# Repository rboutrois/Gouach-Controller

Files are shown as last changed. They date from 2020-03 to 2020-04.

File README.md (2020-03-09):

# Gouach controller

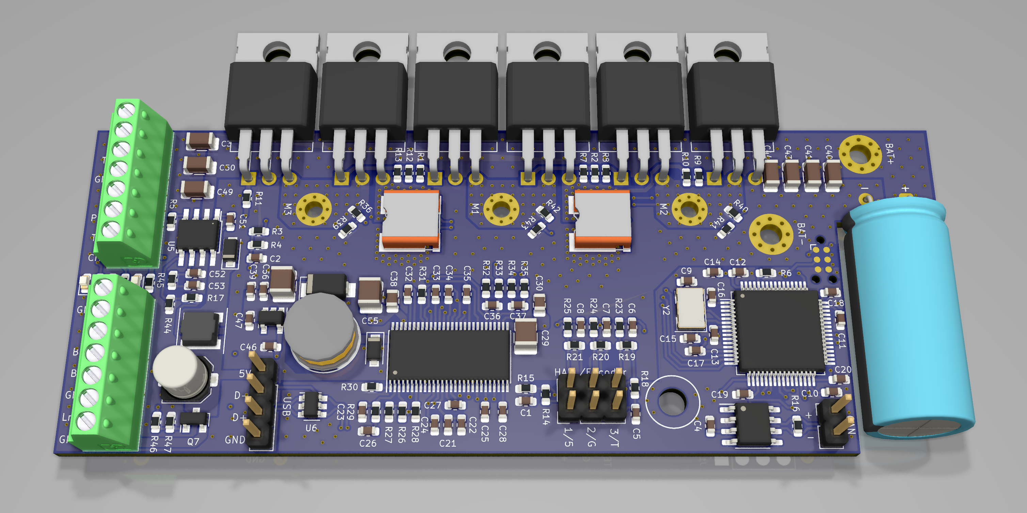
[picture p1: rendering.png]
rendering


## Peripherals pinout
### Throttle
- +5V
- ADC_THROTTLE
- GND

### Torque sensor
- +5V
- PFS
- ADC_TORQUE
- CRUISE
- GND

### Brake
- +5V
- IO_BRAKE
- ADC_BRAKE
- GND

### Motor
3 Phases
- +5V
- HALL_1
- HALL_2
- HALL_3
- TEMPERATURE
- GND

### UART
- +5V
- Tx
- Rx
- GND

### UART
- CAN_H
- CAN_L

### USB
- +5V
- D+
- D-
- GND

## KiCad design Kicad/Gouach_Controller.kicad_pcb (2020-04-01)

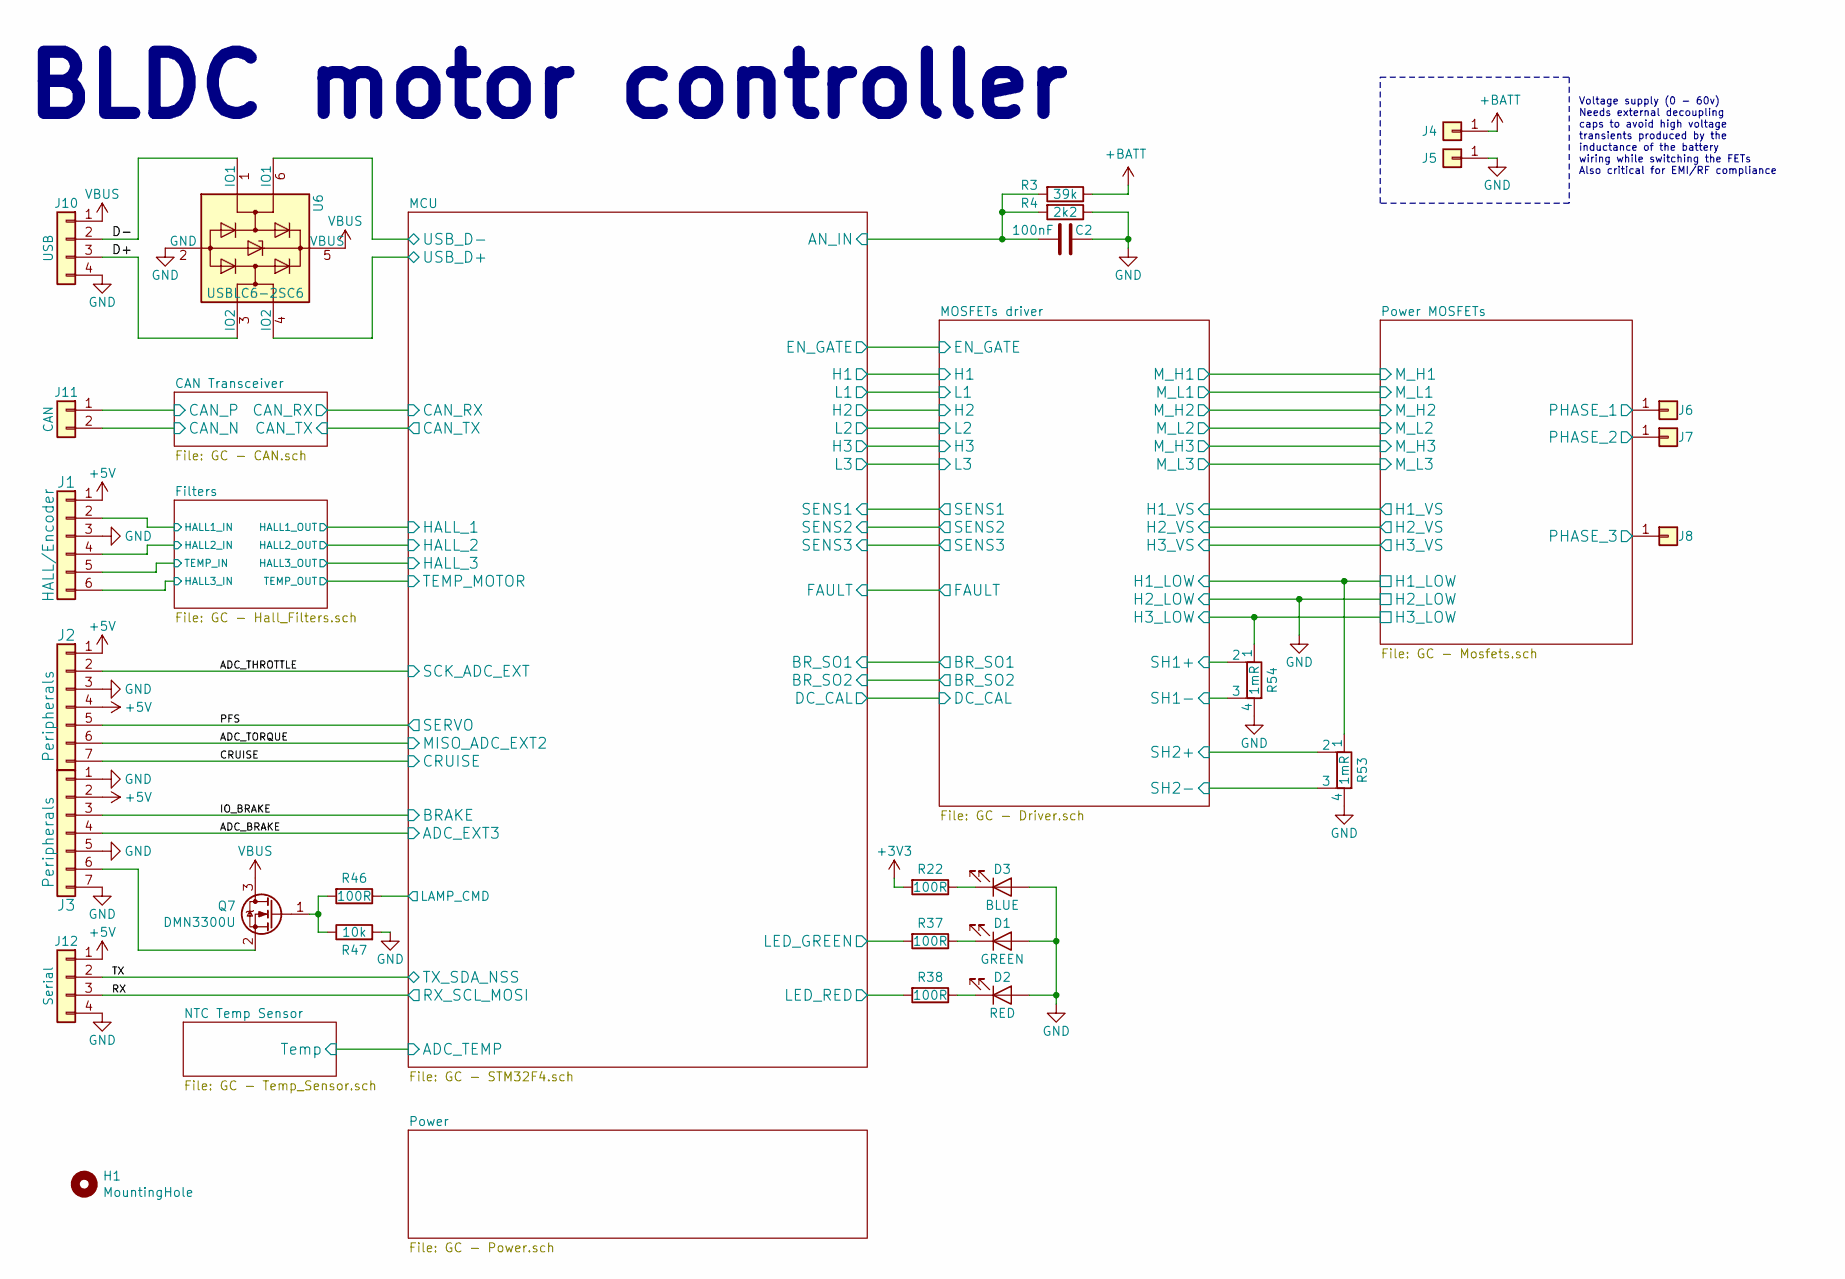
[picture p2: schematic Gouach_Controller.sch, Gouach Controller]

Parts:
C2: 100nF; C_0603_1608Metric
D1: GREEN; LED_0603_1608Metric
D2: RED; LED_0603_1608Metric
D3: BLUE; LED_0603_1608Metric
H1: MountingHole; MountingHole_3.2mm_M3
J1: HALL/Encoder; PinHeader_2x03_P2.54mm_Vertical
J2, J3: Peripherals; TerminalBlock_Phoenix_MPT-2.54mm_7pol
J4: BAT+; MountingHole_2.7mm_Pad_Via
J5: BAT-; MountingHole_2.7mm_Pad_Via
J6: M1; MountingHole_2.2mm_M2_Pad_Via
J7: M2; MountingHole_2.2mm_M2_Pad_Via
J8: M3; MountingHole_2.2mm_M2_Pad_Via
J10: USB; PinHeader_1x04_P2.54mm_Vertical
J11: CAN; PinHeader_1x02_P2.54mm_Vertical
J12: Serial; PinHeader_1x04_P2.54mm_Vertical
Q7: DMN3300U; SOT-23; Mouser 621-DMN3300U-7
R3: 39k; R_0603_1608Metric
R4: 2k2; R_0603_1608Metric
R22, R37, R38, R46: 100R; R_0603_1608Metric
R47: 10k; R_0603_1608Metric
R53, R54: 1mR; WSLP2726; Mouser 71-WSLP27261L000FEA
U6: USBLC6-2SC6; SOT-23-6; Mouser 511-USBLC6-2SC6

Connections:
+3V3: R22.2; also elsewhere on the board
+5V: J1.1, J2.1, J2.4, J3.2, J12.1; also elsewhere on the board
+BATT: J4.1, R3.1; also elsewhere on the board
/ADC_BRAKE: J3.4; also elsewhere on the board
/ADC_THROTTLE: J2.2; also elsewhere on the board
/ADC_TORQUE: J2.6; also elsewhere on the board
/CAN Transceiver/CAN_N: J11.2; also elsewhere on the board
/CAN Transceiver/CAN_P: J11.1; also elsewhere on the board
/CRUISE: J2.7; also elsewhere on the board
/D+: J10.3, U6.3 (IO2)
/D-: J10.2, U6.1 (IO1)
/Filters/HALL1_IN: J1.2; also elsewhere on the board
/Filters/HALL2_IN: J1.4; also elsewhere on the board
/Filters/HALL3_IN: J1.6; also elsewhere on the board
/Filters/TEMP_IN: J1.5; also elsewhere on the board
/IO_BRAKE: J3.3; also elsewhere on the board
/MCU/AN_IN: C2.2, R3.2, R4.2; also elsewhere on the board
/MCU/LAMP_CMD: R46.1; also elsewhere on the board
/MCU/LED_GREEN: R37.2; also elsewhere on the board
/MCU/LED_RED: R38.2; also elsewhere on the board
/MCU/USB_D+: U6.4 (IO2); also elsewhere on the board
/MCU/USB_D-: U6.6 (IO1); also elsewhere on the board
/MOSFETs driver/H1_LOW: R53.1; also elsewhere on the board
/MOSFETs driver/H1_VS: J6.1; also elsewhere on the board
/MOSFETs driver/H2_VS: J7.1; also elsewhere on the board
/MOSFETs driver/H3_LOW: R54.1; also elsewhere on the board
/MOSFETs driver/H3_VS: J8.1; also elsewhere on the board
/MOSFETs driver/SH1+: R54.2; also elsewhere on the board
/MOSFETs driver/SH1-: R54.3; also elsewhere on the board
/MOSFETs driver/SH2+: R53.2; also elsewhere on the board
/MOSFETs driver/SH2-: R53.3; also elsewhere on the board
/PFS: J2.5; also elsewhere on the board
/RX: J12.3; also elsewhere on the board
/TX: J12.2; also elsewhere on the board
GND: C2.1, D1.2 (A), D2.2 (A), D3.2 (A), J1.3, J2.3, J3.1, J3.5, J3.7, J5.1, J10.4, J12.4, R4.1, R47.2, R53.4, R54.4, U6.2 (GND); also elsewhere on the board
unnamed: D1.1 (K), R37.1
unnamed: D2.1 (K), R38.1
unnamed: D3.1 (K), R22.1
unnamed: J3.6, Q7.2 (S)
unnamed: Q7.1 (G), R46.2, R47.1
VBUS: J10.1, Q7.3 (D), U6.5 (VBUS); also elsewhere on the board

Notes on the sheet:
Voltage supply (0 - 60v) Needs external decoupling caps to avoid high voltage transients produced by the inductance of the battery wiring while switching the FETs Also critical for EMI/RF compliance
BLDC motor controller

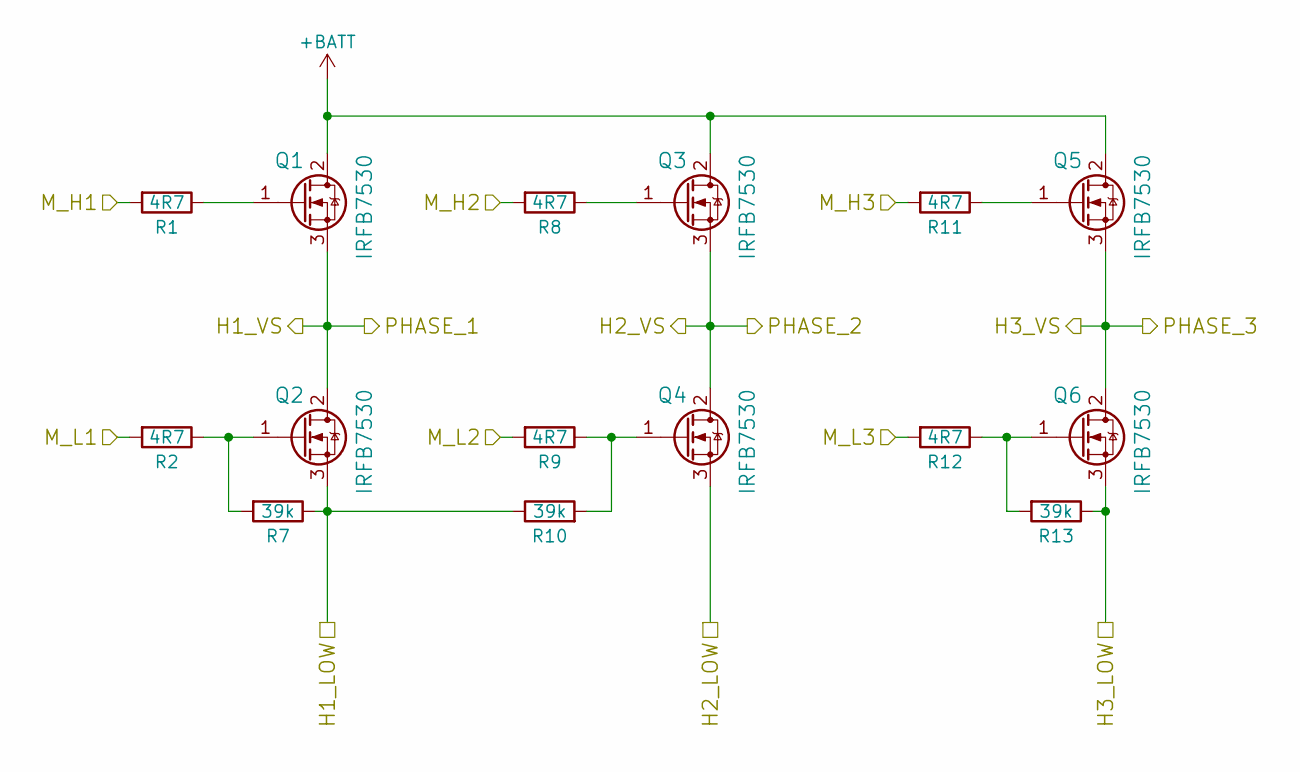
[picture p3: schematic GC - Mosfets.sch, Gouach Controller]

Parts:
Q1, Q2, Q3, Q4, Q5, Q6: IRFB7530; TO-220-3_Horizontal; Mouser 942-IRFB7530PBF
R1, R2, R8, R9, R11, R12: 4R7; R_0603_1608Metric
R7, R10, R13: 39k; R_0603_1608Metric

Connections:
+BATT: Q1.2 (D), Q3.2 (D), Q5.2 (D); also elsewhere on the board
/MOSFETs driver/H1_LOW: Q2.3 (S), R7.1, R10.1; also elsewhere on the board
/MOSFETs driver/H1_VS: Q1.3 (S), Q2.2 (D); also elsewhere on the board
/MOSFETs driver/H2_VS: Q3.3 (S), Q4.2 (D); also elsewhere on the board
/MOSFETs driver/H3_LOW: Q6.3 (S), R13.1; also elsewhere on the board
/MOSFETs driver/H3_VS: Q5.3 (S), Q6.2 (D); also elsewhere on the board
/MOSFETs driver/M_H1: R1.2; also elsewhere on the board
/MOSFETs driver/M_H2: R8.2; also elsewhere on the board
/MOSFETs driver/M_H3: R11.2; also elsewhere on the board
/MOSFETs driver/M_L1: R2.2; also elsewhere on the board
/MOSFETs driver/M_L2: R9.2; also elsewhere on the board
/MOSFETs driver/M_L3: R12.2; also elsewhere on the board
GND: Q4.3 (S); also elsewhere on the board
unnamed: Q1.1 (G), R1.1
unnamed: Q2.1 (G), R2.1, R7.2
unnamed: Q3.1 (G), R8.1
unnamed: Q4.1 (G), R9.1, R10.2
unnamed: Q5.1 (G), R11.1
unnamed: Q6.1 (G), R12.1, R13.2

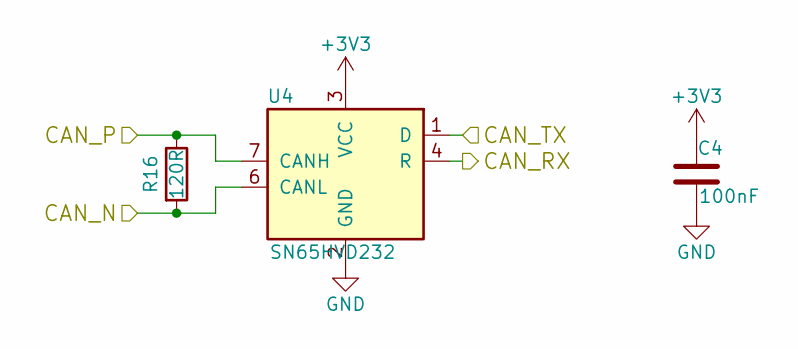
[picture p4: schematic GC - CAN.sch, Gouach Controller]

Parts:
C4: 100nF; C_0603_1608Metric
R16: 120R; R_0603_1608Metric
U4: SN65HVD232; SOIC-8_3.9x4.9mm_P1.27mm; Mouser 595-SN65HVD232DR

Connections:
+3V3: C4.1, U4.3 (VCC); also elsewhere on the board
/CAN Transceiver/CAN_N: R16.2, U4.6 (CANL); also elsewhere on the board
/CAN Transceiver/CAN_P: R16.1, U4.7 (CANH); also elsewhere on the board
/CAN Transceiver/CAN_RX: U4.4 (R); also elsewhere on the board
/CAN Transceiver/CAN_TX: U4.1 (D); also elsewhere on the board
GND: C4.2, U4.2 (GND); also elsewhere on the board

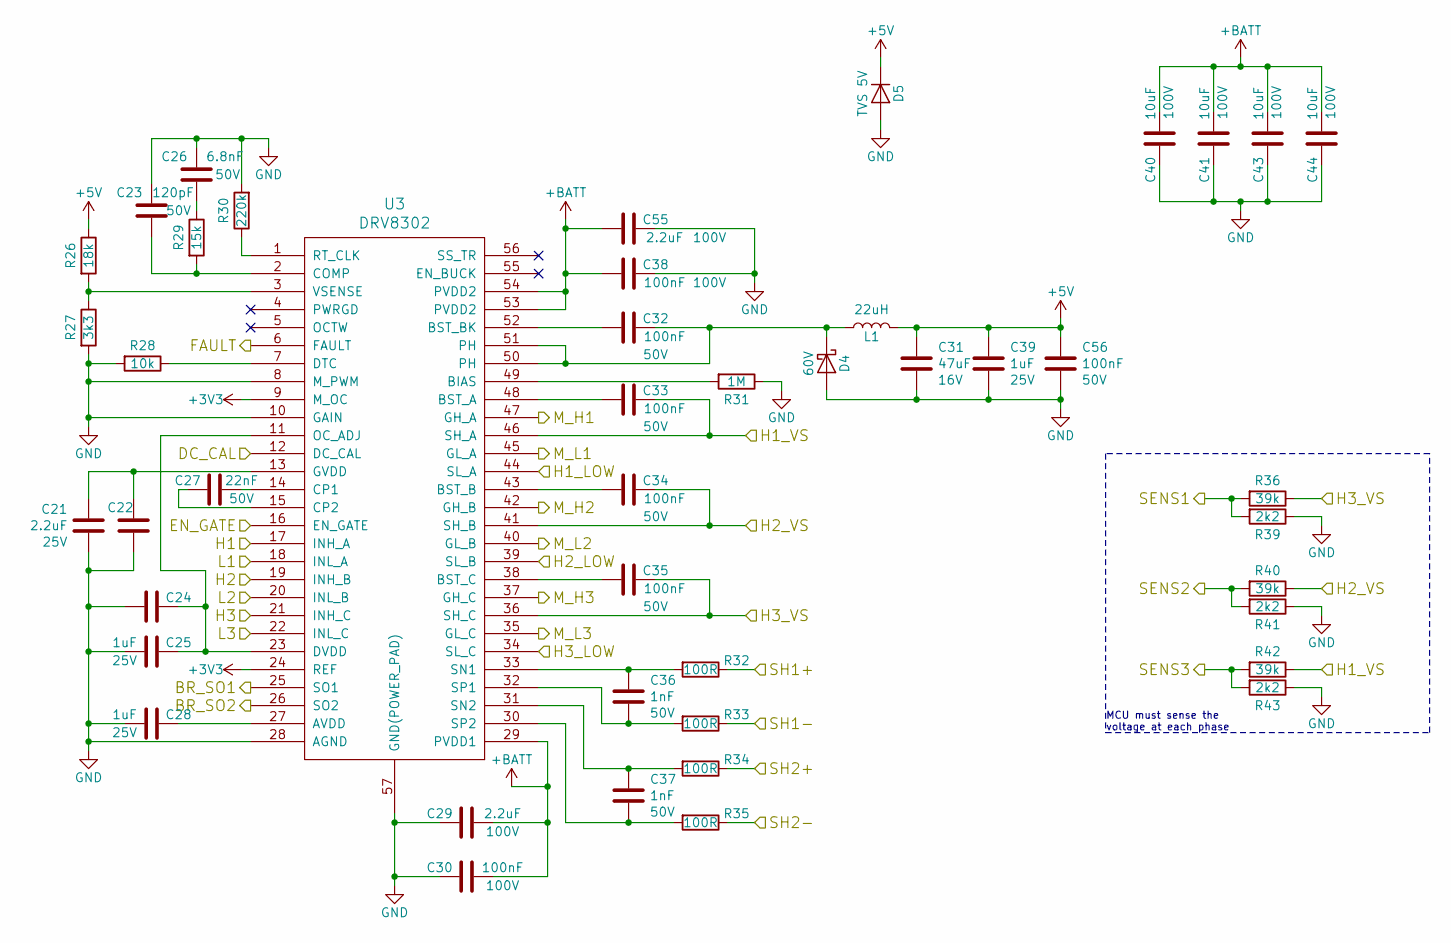
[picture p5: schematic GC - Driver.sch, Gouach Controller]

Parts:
C21: 2.2uF; C_0603_1608Metric
C22, C24: C_0603_1608Metric
C23: 120pF; C_0603_1608Metric
C25, C28, C39: 1uF; C_0603_1608Metric
C26: 6.8nF; C_0603_1608Metric
C27: 22nF; C_0603_1608Metric
C29, C55: 2.2uF; C_1210_3225Metric
C30, C38: 100nF; C_0805_2012Metric
C31: 47uF; C_1210_3225Metric
C32, C33, C34, C35, C56: 100nF; C_0603_1608Metric
C36, C37: 1nF; C_0603_1608Metric
C40, C41, C43, C44: 10uF; C_1206_3216Metric
D4: 60V; D_SOD-123F; Mouser 771-PMEG6020ER-115
D5: TVS 5V; D_SMA; Mouser 652-SMAJ5.0A
L1: 22uH; SDR0805; Mouser 652-SDR0805-220ML
R26: 18k; R_0603_1608Metric
R27: 3k3; R_0603_1608Metric
R28: 10k; R_0603_1608Metric
R29: 15k; R_0603_1608Metric
R30: 220k; R_0603_1608Metric
R31: 1M; R_0603_1608Metric
R32, R33, R34, R35: 100R; R_0603_1608Metric
R36, R40, R42: 39k; R_0603_1608Metric
R39, R41, R43: 2k2; R_0603_1608Metric
U3: DRV8302; Mouser 595-DRV8302DCA

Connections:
+3V3: U3.9 (M_OC), U3.24 (REF); also elsewhere on the board
+5V: C31.1, C39.1, C56.1, D5.1 (K), L1.2, R26.1; also elsewhere on the board
+BATT: C29.1, C30.1, C38.2, C40.1, C41.1, C43.1, C44.1, C55.2, U3.29 (PVDD1), U3.53 (PVDD2), U3.54 (PVDD2); also elsewhere on the board
/MCU/BR_SO1: U3.25 (SO1); also elsewhere on the board
/MCU/BR_SO2: U3.26 (SO2); also elsewhere on the board
/MCU/DC_CAL: U3.12 (DC_CAL); also elsewhere on the board
/MCU/EN_GATE: U3.16 (EN_GATE); also elsewhere on the board
/MCU/FAULT: U3.6 (FAULT); also elsewhere on the board
/MCU/H1: U3.17 (INH_A); also elsewhere on the board
/MCU/H2: U3.19 (INH_B); also elsewhere on the board
/MCU/H3: U3.21 (INH_C); also elsewhere on the board
/MCU/L1: U3.18 (INL_A); also elsewhere on the board
/MCU/L2: U3.20 (INL_B); also elsewhere on the board
/MCU/L3: U3.22 (INL_C); also elsewhere on the board
/MCU/SENS1: R36.2, R39.2; also elsewhere on the board
/MCU/SENS2: R40.2, R41.2; also elsewhere on the board
/MCU/SENS3: R42.2, R43.2; also elsewhere on the board
/MOSFETs driver/H1_LOW: U3.44 (SL_A); also elsewhere on the board
/MOSFETs driver/H1_VS: C33.1, R42.1, U3.46 (SH_A); also elsewhere on the board
/MOSFETs driver/H2_VS: C34.1, R40.1, U3.41 (SH_B); also elsewhere on the board
/MOSFETs driver/H3_LOW: U3.34 (SL_C); also elsewhere on the board
/MOSFETs driver/H3_VS: C35.1, R36.1, U3.36 (SH_C); also elsewhere on the board
/MOSFETs driver/M_H1: U3.47 (GH_A); also elsewhere on the board
/MOSFETs driver/M_H2: U3.42 (GH_B); also elsewhere on the board
/MOSFETs driver/M_H3: U3.37 (GH_C); also elsewhere on the board
/MOSFETs driver/M_L1: U3.45 (GL_A); also elsewhere on the board
/MOSFETs driver/M_L2: U3.40 (GL_B); also elsewhere on the board
/MOSFETs driver/M_L3: U3.35 (GL_C); also elsewhere on the board
/MOSFETs driver/SH1+: R32.1; also elsewhere on the board
/MOSFETs driver/SH1-: R33.1; also elsewhere on the board
/MOSFETs driver/SH2+: R34.1; also elsewhere on the board
/MOSFETs driver/SH2-: R35.1; also elsewhere on the board
GND: C21.2, C22.2, C23.1, C24.1, C25.1, C26.1, C28.1, C29.2, C30.2, C31.2, C38.1, C39.2, C40.2, C41.2, C43.2, C44.2, C55.1, C56.2, D4.2 (A), D5.2 (A), R27.2, R28.2, R30.2, R31.1, R39.1, R41.1, R43.1, U3.8 (M_PWM), U3.10 (GAIN), U3.28 (AGND), U3.39 (SL_B), U3.57 (GND(POWER_PAD)); also elsewhere on the board
unnamed: C21.1, C22.1, U3.13 (GVDD)
unnamed: C23.2, R29.2, U3.2 (COMP)
unnamed: C24.2, C25.2, U3.11 (OC_ADJ), U3.23 (DVDD)
unnamed: C26.2, R29.1
unnamed: C27.1, U3.14 (CP1)
unnamed: C27.2, U3.15 (CP2)
unnamed: C28.2, U3.27 (AVDD)
unnamed: C32.1, D4.1 (K), L1.1, U3.50 (PH), U3.51 (PH)
unnamed: C32.2, U3.52 (BST_BK)
unnamed: C33.2, U3.48 (BST_A)
unnamed: C34.2, U3.43 (BST_B)
unnamed: C35.2, U3.38 (BST_C)
unnamed: C36.1, R32.2, U3.33 (SN1)
unnamed: C36.2, R33.2, U3.32 (SP1)
unnamed: C37.1, R34.2, U3.31 (SN2)
unnamed: C37.2, R35.2, U3.30 (SP2)
unnamed: R26.2, R27.1, U3.3 (VSENSE)
unnamed: R28.1, U3.7 (DTC)
unnamed: R30.1, U3.1 (RT_CLK)
unnamed: R31.2, U3.49 (BIAS)

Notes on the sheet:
MCU must sense the voltage at each phase

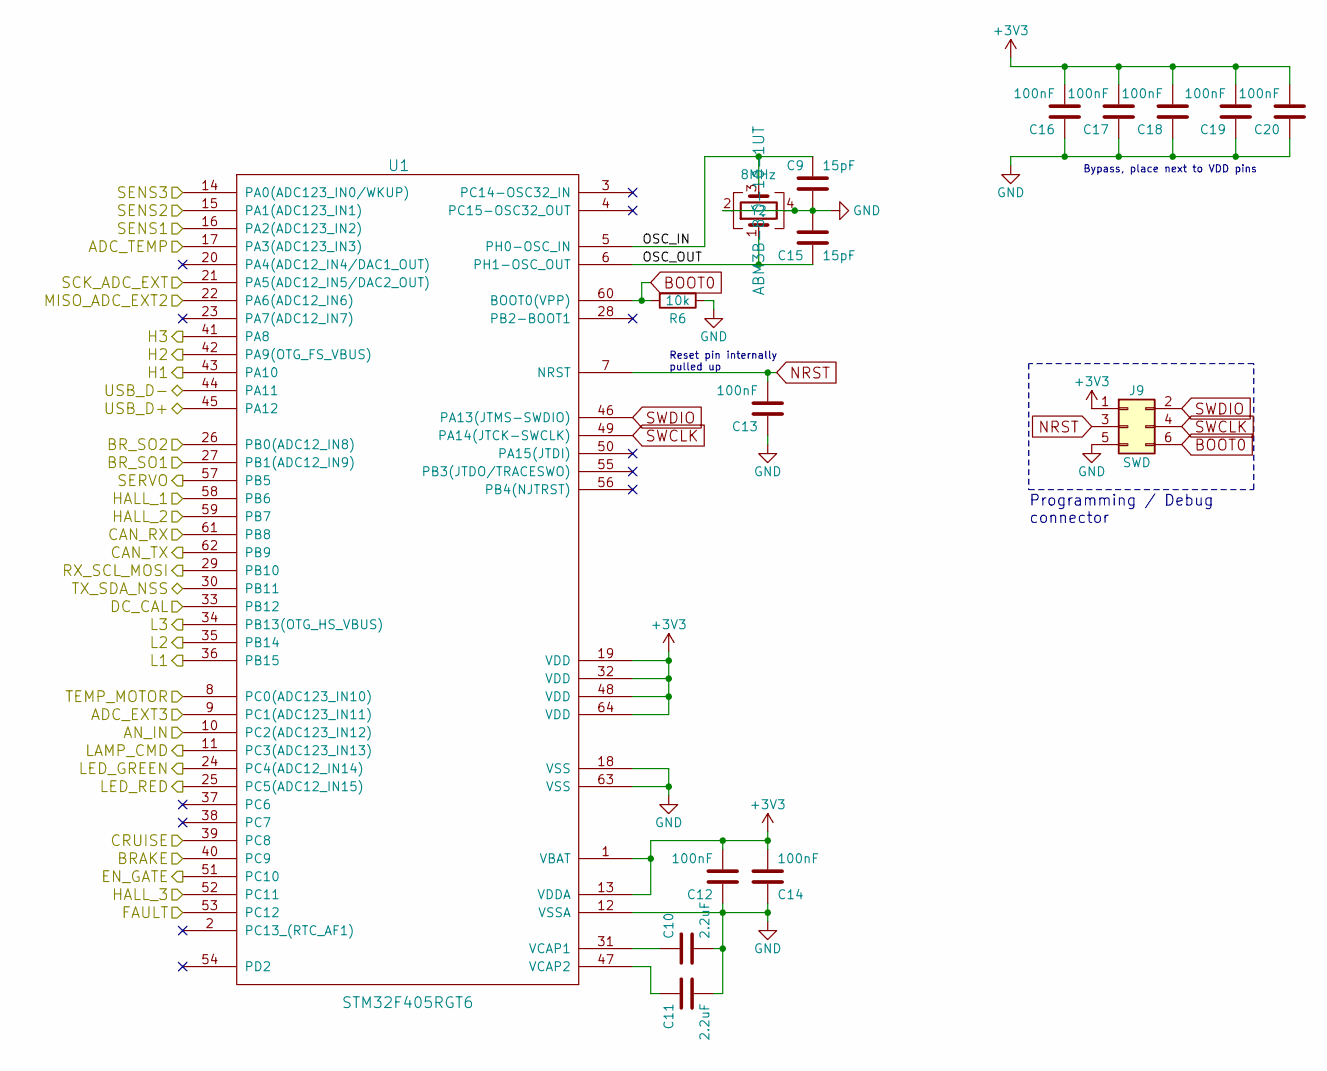
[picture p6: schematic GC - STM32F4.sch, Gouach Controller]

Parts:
C9, C15: 15pF; C_0603_1608Metric
C10, C11: 2.2uF; C_0603_1608Metric
C12, C13, C14, C16, C17, C18, C19, C20: 100nF; C_0603_1608Metric
J9: SWD; Tag-Connect_TC2030-IDC-NL_2x03_P1.27mm_Vertical
R6: 10k; R_0603_1608Metric
U1: STM32F405RGT6; LQFP-64_10x10mm_P0.5mm; Mouser 511-STM32F405RGT6
Y2: 8MHz; Crystal_SMD_5032-4Pin_5.0x3.2mm; Mouser 815-ABM3B-8.0-10-1UT

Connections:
+3V3: C12.2, C14.2, C16.2, C17.2, C18.2, C19.2, C20.2, J9.1, U1.1 (VBAT), U1.13 (VDDA), U1.19 (VDD), U1.32 (VDD), U1.48 (VDD), U1.64 (VDD); also elsewhere on the board
/ADC_BRAKE: U1.9 (PC1(ADC123_IN11)); also elsewhere on the board
/ADC_THROTTLE: U1.21 (PA5(ADC12_IN5/DAC2_OUT)); also elsewhere on the board
/ADC_TORQUE: U1.22 (PA6(ADC12_IN6)); also elsewhere on the board
/CAN Transceiver/CAN_RX: U1.61 (PB8); also elsewhere on the board
/CAN Transceiver/CAN_TX: U1.62 (PB9); also elsewhere on the board
/CRUISE: U1.39 (PC8); also elsewhere on the board
/Filters/HALL1_OUT: U1.58 (PB6); also elsewhere on the board
/Filters/HALL2_OUT: U1.59 (PB7); also elsewhere on the board
/Filters/HALL3_OUT: U1.52 (PC11); also elsewhere on the board
/Filters/TEMP_IN: U1.8 (PC0(ADC123_IN10)); also elsewhere on the board
/IO_BRAKE: U1.40 (PC9); also elsewhere on the board
/MCU/ADC_TEMP: U1.17 (PA3(ADC123_IN3)); also elsewhere on the board
/MCU/AN_IN: U1.10 (PC2(ADC123_IN12)); also elsewhere on the board
/MCU/BR_SO1: U1.27 (PB1(ADC12_IN9)); also elsewhere on the board
/MCU/BR_SO2: U1.26 (PB0(ADC12_IN8)); also elsewhere on the board
/MCU/DC_CAL: U1.33 (PB12); also elsewhere on the board
/MCU/EN_GATE: U1.51 (PC10); also elsewhere on the board
/MCU/FAULT: U1.53 (PC12); also elsewhere on the board
/MCU/H1: U1.43 (PA10); also elsewhere on the board
/MCU/H2: U1.42 (PA9(OTG_FS_VBUS)); also elsewhere on the board
/MCU/H3: U1.41 (PA8); also elsewhere on the board
/MCU/L1: U1.36 (PB15); also elsewhere on the board
/MCU/L2: U1.35 (PB14); also elsewhere on the board
/MCU/L3: U1.34 (PB13(OTG_HS_VBUS)); also elsewhere on the board
/MCU/LAMP_CMD: U1.11 (PC3(ADC123_IN13)); also elsewhere on the board
/MCU/LED_GREEN: U1.24 (PC4(ADC12_IN14)); also elsewhere on the board
/MCU/LED_RED: U1.25 (PC5(ADC12_IN15)); also elsewhere on the board
/MCU/OSC_IN: C9.1, U1.5 (PH0-OSC_IN), Y2.3
/MCU/OSC_OUT: C15.2, U1.6 (PH1-OSC_OUT), Y2.1
/MCU/SENS1: U1.16 (PA2(ADC123_IN2)); also elsewhere on the board
/MCU/SENS2: U1.15 (PA1(ADC123_IN1)); also elsewhere on the board
/MCU/SENS3: U1.14 (PA0(ADC123_IN0/WKUP)); also elsewhere on the board
/MCU/USB_D+: U1.45 (PA12); also elsewhere on the board
/MCU/USB_D-: U1.44 (PA11); also elsewhere on the board
/PFS: U1.57 (PB5); also elsewhere on the board
/RX: U1.29 (PB10); also elsewhere on the board
/TX: U1.30 (PB11); also elsewhere on the board
BOOT0: J9.6, R6.2, U1.60 (BOOT0(VPP))
GND: C9.2, C10.2, C11.2, C12.1, C13.1, C14.1, C15.1, C16.1, C17.1, C18.1, C19.1, C20.1, J9.5, R6.1, U1.12 (VSSA), U1.18 (VSS), U1.63 (VSS), Y2.2, Y2.4; also elsewhere on the board
NRST: C13.2, J9.3, U1.7 (NRST)
unnamed: C10.1, U1.31 (VCAP1)
unnamed: C11.1, U1.47 (VCAP2)
SWCLK: J9.4, U1.49 (PA14(JTCK-SWCLK))
SWDIO: J9.2, U1.46 (PA13(JTMS-SWDIO))

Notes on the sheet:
Programming / Debug connector
Reset pin internally pulled up
Bypass, place next to VDD pins

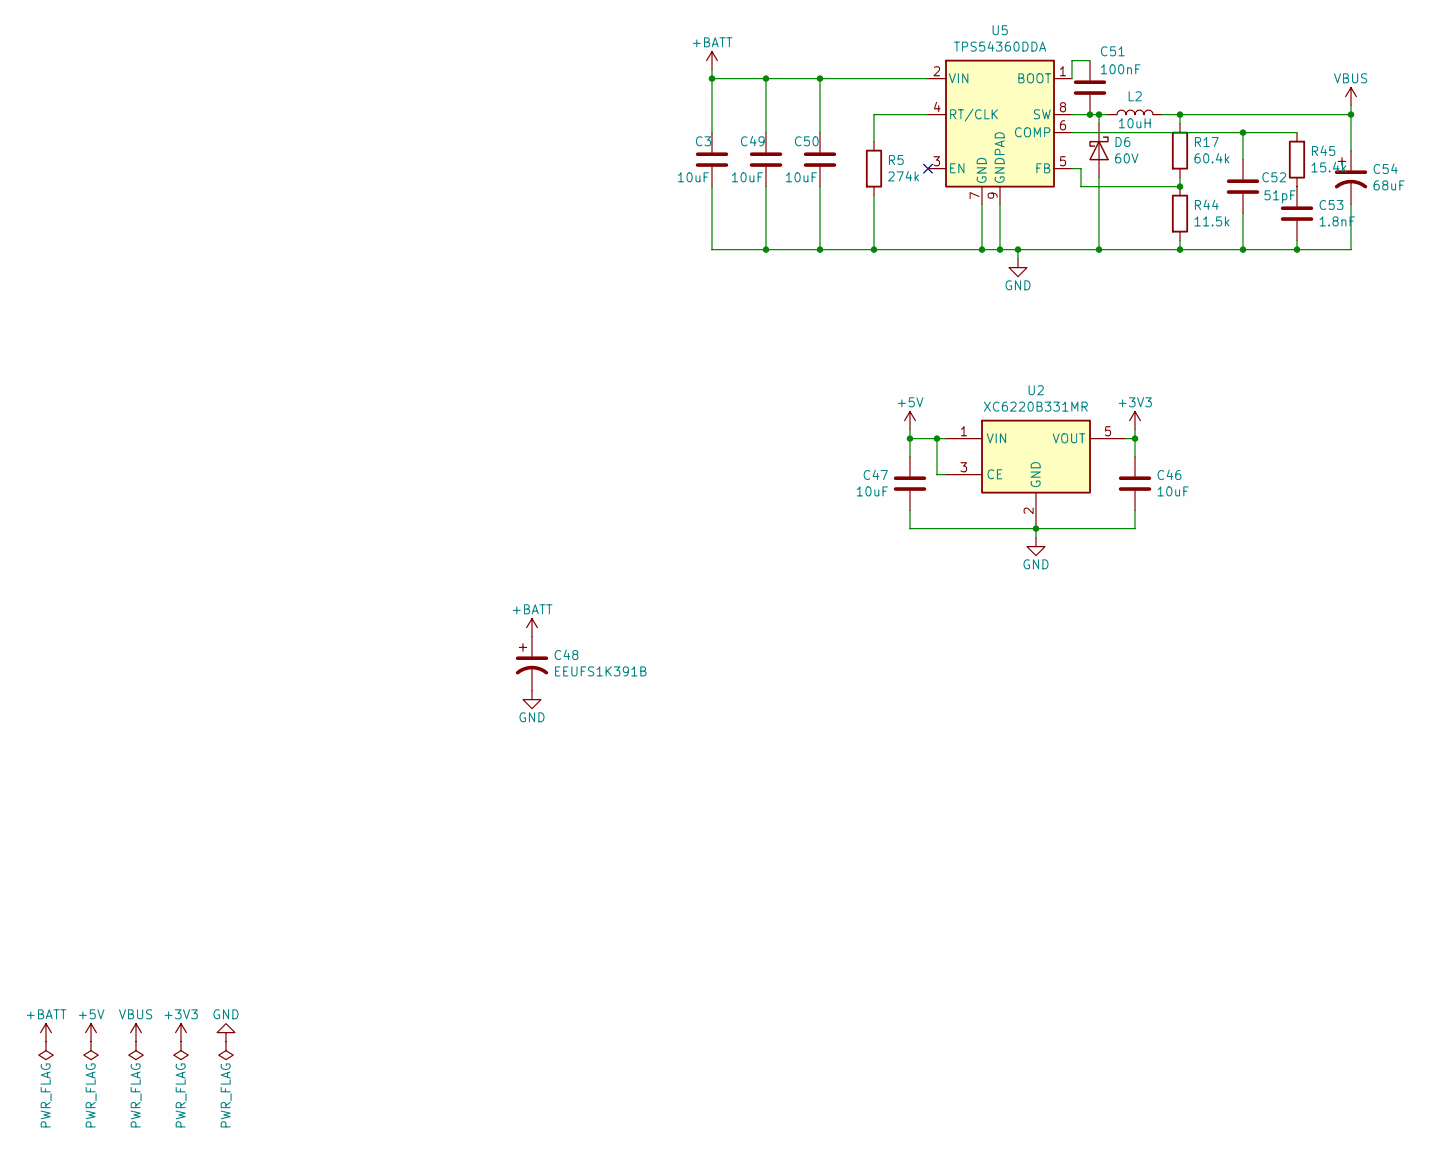
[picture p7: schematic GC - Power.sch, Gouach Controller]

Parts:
C3, C49, C50: 10uF; C_1206_3216Metric
C46, C47: 10uF; C_0603_1608Metric
C48: EEUFS1K391B; Capacitor_Horizontal
C51: 100nF; C_0603_1608Metric
C52: 51pF; C_0603_1608Metric
C53: 1.8nF; C_0603_1608Metric
C54: 68uF; C_Elec_5x5.8
D6: 60V; D_SOD-123F; Mouser 771-PMEG6020ER-115
L2: 10uH; L_Coilcraft_XAL5030; Mouser 994-XAL5050-103MEB
R5: 274k; R_0603_1608Metric
R17: 60.4k; R_0603_1608Metric
R44: 11.5k; R_0603_1608Metric
R45: 15.4k; R_0603_1608Metric
U2: XC6220B331MR; SOT-23-5; Mouser 865-XC6220B331MR-G
U5: TPS54360DDA; TI_SO-PowerPAD-8; Mouser 595-TPS54360DDA

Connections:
+3V3: C46.1, U2.5 (VOUT); also elsewhere on the board
+5V: C47.1, U2.1 (VIN), U2.3 (CE); also elsewhere on the board
+BATT: C3.1, C48.1, C49.1, C50.1, U5.2 (VIN); also elsewhere on the board
GND: C3.2, C46.2, C47.2, C48.2, C49.2, C50.2, C52.2, C53.2, C54.2, D6.2 (A), R5.2, R44.2, U2.2 (GND), U5.7 (GND), U5.9 (GNDPAD); also elsewhere on the board
unnamed: C51.1, U5.1 (BOOT)
unnamed: C51.2, D6.1 (K), L2.1, U5.8 (SW)
unnamed: C52.1, R45.2, U5.6 (COMP)
unnamed: C53.1, R45.1
unnamed: R5.1, U5.4 (RT/CLK)
unnamed: R17.2, R44.1, U5.5 (FB)
VBUS: C54.1, L2.2, R17.1; also elsewhere on the board

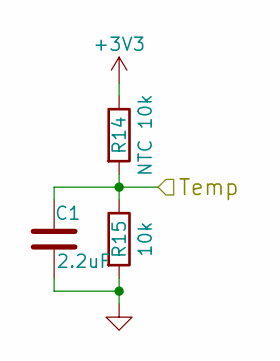
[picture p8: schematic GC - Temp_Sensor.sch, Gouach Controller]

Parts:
C1: 2.2uF; C_0603_1608Metric
R14: NTC 10k; R_0603_1608Metric
R15: 10k; R_0603_1608Metric

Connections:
+3V3: R14.1; also elsewhere on the board
/MCU/ADC_TEMP: C1.1, R14.2, R15.1; also elsewhere on the board
GND: C1.2, R15.2; also elsewhere on the board

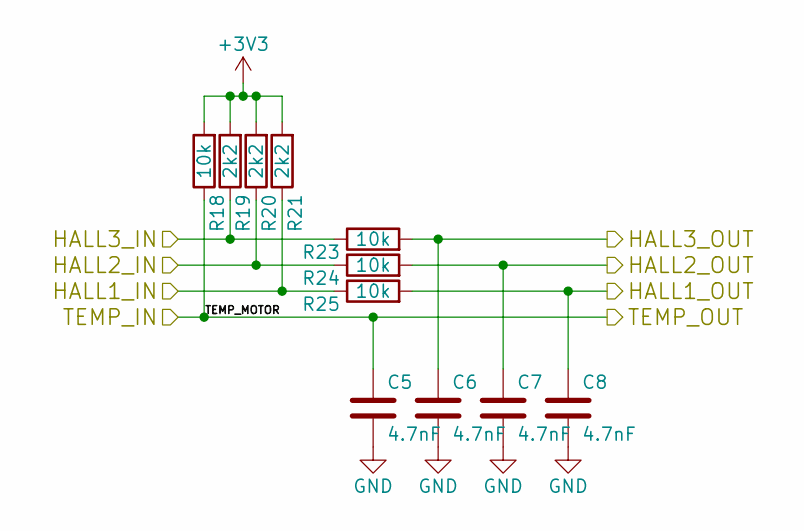
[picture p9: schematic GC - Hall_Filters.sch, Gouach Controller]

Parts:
C5, C6, C7, C8: 4.7nF; C_0603_1608Metric
R18, R23, R24, R25: 10k; R_0603_1608Metric
R19, R20, R21: 2k2; R_0603_1608Metric

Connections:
+3V3: R18.2, R19.2, R20.2, R21.2; also elsewhere on the board
/Filters/HALL1_IN: R21.1, R25.1; also elsewhere on the board
/Filters/HALL1_OUT: C8.1, R25.2; also elsewhere on the board
/Filters/HALL2_IN: R20.1, R24.1; also elsewhere on the board
/Filters/HALL2_OUT: C7.1, R24.2; also elsewhere on the board
/Filters/HALL3_IN: R19.1, R23.1; also elsewhere on the board
/Filters/HALL3_OUT: C6.1, R23.2; also elsewhere on the board
/Filters/TEMP_IN: C5.1, R18.1; also elsewhere on the board
GND: C5.2, C6.2, C7.2, C8.2; also elsewhere on the board

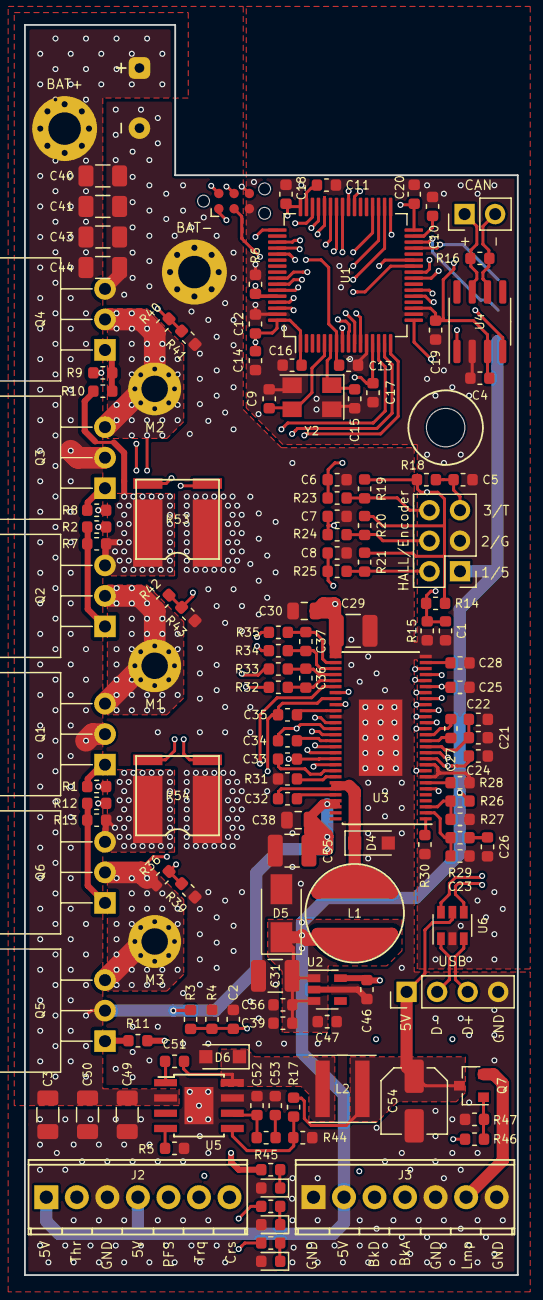
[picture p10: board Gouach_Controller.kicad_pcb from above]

Board: 4 copper layers, 41.0 x 104.0 mm, 138 parts (1 on the bottom side), 107 nets.

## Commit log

2020-02-18 Components Placement
    [GC - CAN.sch, GC - Driver.sch, GC - Hall_Filters.sch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]
2020-02-20 Passives changed from 0805 to 0603
    [GC - CAN.sch, GC - Driver.sch, GC - Hall_Filters.sch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]
2020-02-22 Components placed
    [GC - Driver.sch, GC - Hall_Filters.sch, GC - Mosfets.sch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]
2020-03-03 Adjusting capacitor size/value
    [GC - CAN.sch, GC - Driver.sch, GC - Hall_Filters.sch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]
2020-03-03 Routing done
    [Gouach_Controller.kicad_pcb]
2020-03-03 Adjusted cap size/value + add ESD protection on USB
    [Gouach_Controller.sch]
2020-03-09 Fixed libraries issues
    [GC - CAN.sch, GC - Driver.sch, GC - Hall_Filters.sch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]
2020-03-09 Add Mouser order number
    [GC - CAN.sch, GC - Driver.sch, GC - Mosfets.sch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]
2020-04-01 Add capacitor ref
    [GC - Power.sch]
2020-04-01 Change R22 value
    [Gouach_Controller.sch]
2020-04-01 Add HTML BOM
    [Gouach_Controller.kicad_pcb]
